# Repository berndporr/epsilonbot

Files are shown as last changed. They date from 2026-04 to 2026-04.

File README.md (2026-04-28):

# The Zeta-bot

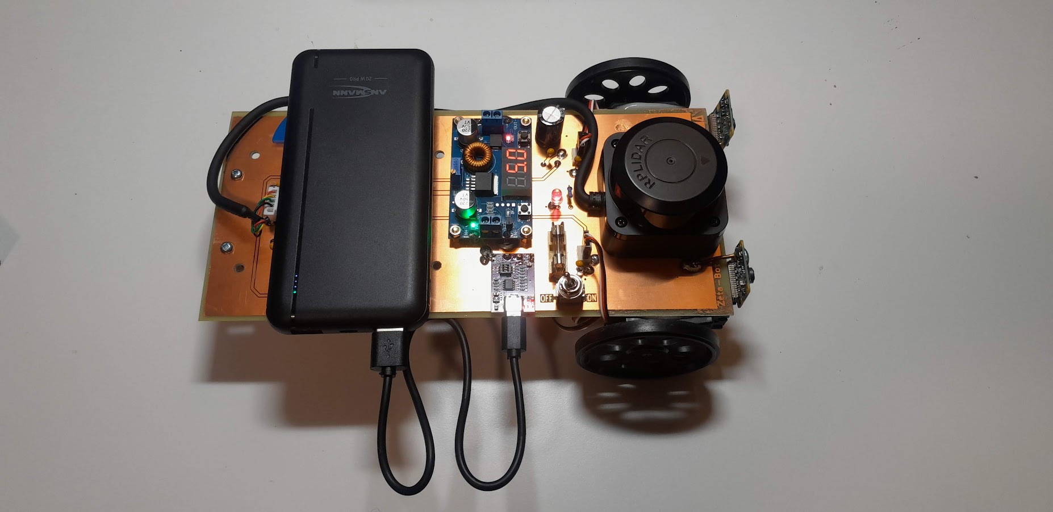
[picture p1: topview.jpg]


What is the Zeta-Bot?

The Zeta-Bot is an open-source robot platform that uses the:

 - Raspberry PI 5,
 - [Parallax's Continuous Rotation Servo Motors](https://www.parallax.com/product/parallax-continuous-rotation-servo/),
 - [C1 LIDAR](https://www.slamtec.com/en/c1),
 - two [Raspberry PI V2 cameras](https://www.raspberrypi.com/products/camera-module-v2/) for stereo vision,
 - [a standard mobile phone 1700mAh power bank](https://uk.rs-online.com/web/p/power-banks/2498449).

It's based on years and years of experience making single PCB
Raspberry PI based robots. Every part has been chosen because of
extensive lab use proving its reliability over the years and because
of its solid hard- and software support.

## Hardware

The KiCad design files and BOM are in [hardware](hardware).

## Software

It's all in C++! Both cameras and LIDAR have an event driven framework with callbacks so no loops and multi-threaded by design.

 - The motor control libraries are in [wheeleddrive](wheeleddrive).
 - The cameras driver is in https://github.com/berndporr/libcamera2opencv with a demo to display one camera and in [stereo](stereo) is a QT6 based stereo viewer and disparity detector.
 - The LIDAR driver is in https://github.com/berndporr/c1lidar

## Credits

 - (c) 2026, Bernd Porr, mail@berndporr.me.uk
 - (c) 2025, Saleh AlMulla
 - (c) 2025, Yixuan Zha

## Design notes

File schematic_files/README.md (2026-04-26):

# Schematic files

It's been designed by KiCad 10.

The design at the moment is according to GU's workshop requirements who cannot do solderstop and need 2mm pads.

The [bom](bom.pdf) is here.

The Linear servos are simply glued with epoxy onto the PCB.

The RPI V2 cameras are soldered on the ground plane of the PCB with two stiff 6mm wires. There seem to be no sensible camera holders about so stiff wires seem to be the best option also to adjust the cameras for stereo.

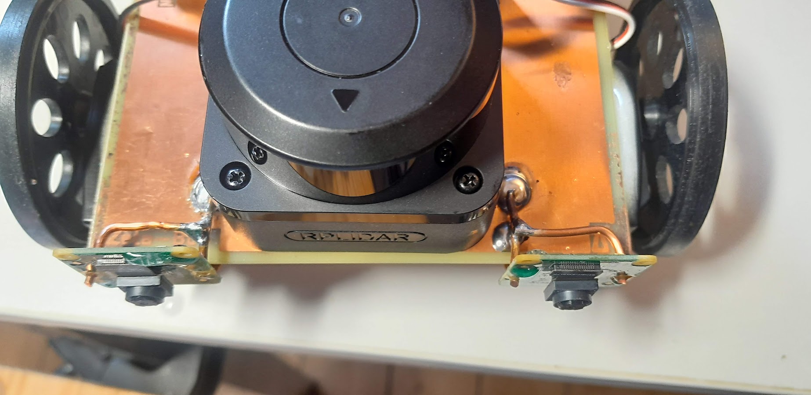
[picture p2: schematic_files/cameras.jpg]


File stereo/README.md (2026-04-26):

# Stereoviewer

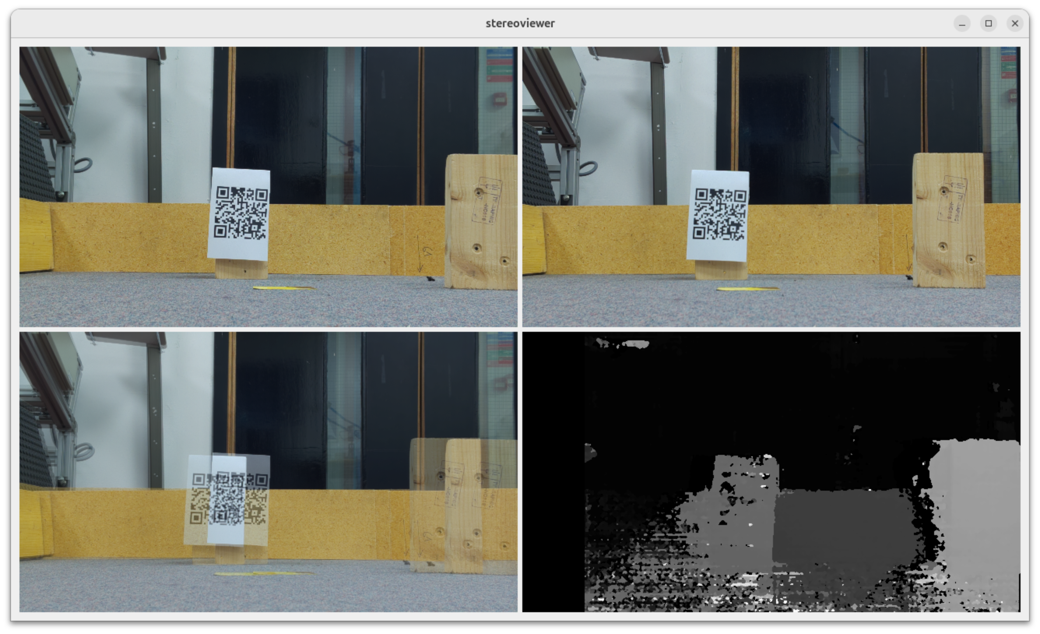
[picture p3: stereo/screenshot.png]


Simple QT6 demo application which captures from both cameras and then calculates
the disparity map.

## Prerequisites

```
apt install libopencv-dev libcamera-dev libturbojpeg0-dev
```

## Compilation

```
cmake .
make
```

## How to run

```
./stereoviewer
```

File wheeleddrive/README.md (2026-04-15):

# C++ ZetaBot API for the Raspberry PI 5

## Prerequisites

Add to `/boot/firmware/config.txt`:

```
dtoverlay=pwm-2chan
```

and reboot.

Check with:

```
pinctrl -p
```

that you see:

```
12: a3    pd | lo // GPIO18 = PWM0_CHAN2
35: a3    pd | lo // GPIO19 = PWM0_CHAN3
```

which corresponds to the sysfs files:

```
/sys/class/pwm/pwmchip0/pwm2: GPIO18 
/sys/class/pwm/pwmchip0/pwm3: GPIO19
```

### libgpiod

The GPIO pins are accessed via the C++ API of the `libgpiod`:

```
apt-get install libgpiod-dev
```

### ncurses

This is needed for testIO for a very simple ASCII GUI!

```
apt-get install libncurses-dev
```

## Building

The built system is `cmake`. Just type:
```
cmake .
make
sudo make install
```

## Usage

### Motor speed

Setting the speeds of the left/right wheels:
```
setLeftWheelSpeed(float speed);
setRightWheelSpeed(float speed);
```
where speed is between -1 and +1.

## Demo programs

 - `testIO` is a simple text GUI program to control the motors.
 - `testMotor` ramps up the motor speed and back again.

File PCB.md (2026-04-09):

# DeltaBot PCB Overview

The DeltaBot PCB was designed in **KiCad** with a double-sided layer layout. The design integrates key subsystems including the **Radxa ROCK 5B**, LiDAR sensor, camera module, and servo motors.

<p align="center">
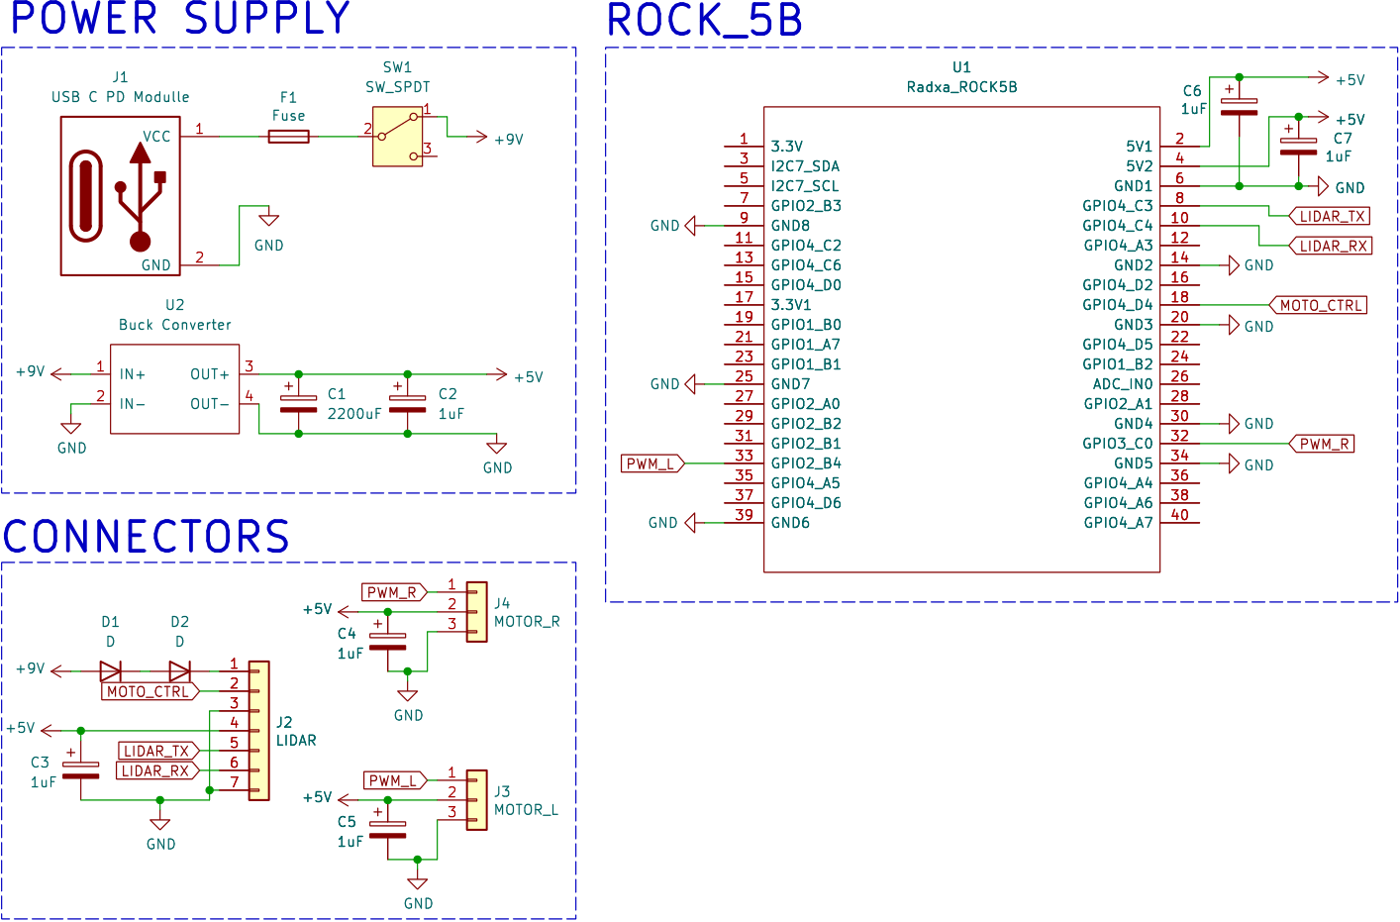
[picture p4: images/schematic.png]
  
</p>

---

## Power System
- Powered via **USB-C Power Delivery (PD)** module at **9V**, stepped down to **5V** using a **DC-DC buck converter**
- A **3.15A fuse** protects against overcurrent
- An **SPDT switch** provides manual ON/OFF control
- A **2200 µF capacitor** suppresses 5V rail ripple for improved voltage stability
- **1 uF** blocking capacitors between each POWER & GND

---

## PCB Layout (Front & Back Layers)

<p align="center">
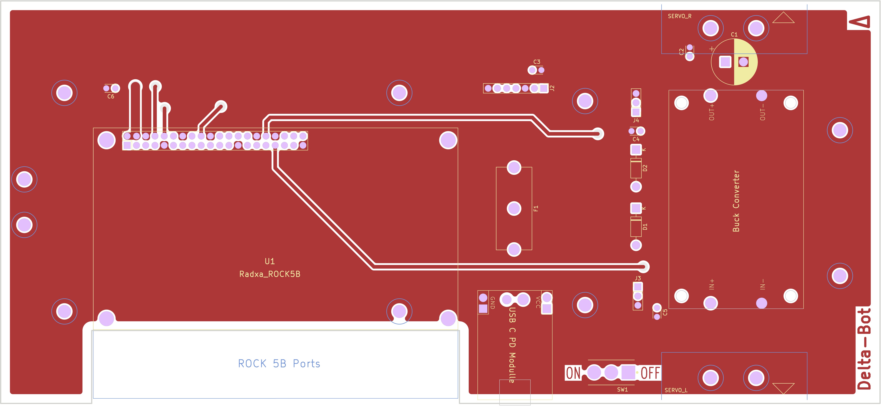
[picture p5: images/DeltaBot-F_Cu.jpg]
  
</p>
<p align="center">
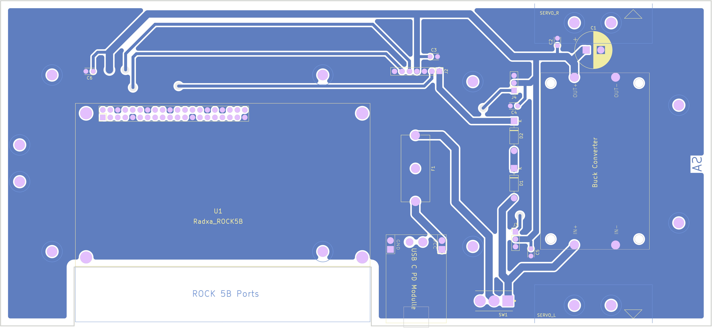
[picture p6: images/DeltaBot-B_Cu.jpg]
  
</p>

---

## ROCK 5B GPIO Pin Assignments

| Function | GPIO Pin(s) | Description |
|---|---|---|
| +5V Power | 2, 4 | Supplies power to board |
| GND | Multiple | Ground reference |
| UART_TX | 8 | TX to LiDAR's RX |
| UART_RX | 10 | RX from LiDAR's TX |
| NC | 18 | NC |
| PWM_L | 32 | PWM control for left servo |
| PWM_R | 33 | PWM control for right servo |

To change or add to the layout, check [here](https://wiki.radxa.com/Rock5/hardware/5b/gpio) for the rock's gpio connections.

---

## Connectors

- **J2 (LiDAR)**: 7-pin Molex
  - UART (TX/RX), 5V & 8.34V power lines
- **J3 / J4 (Servo Motors)**: 3-pin headers  
  - 5V, GND, PWM (Left/Right)

---

## Files

- [Full Schematic](schematic_files/DeltaBot.kicad_sch)
- [PCB Design](schematic_files/DeltaBot.kicad_pcb)
- [PCB Footprints](schematic_files/deltabot.pretty.zip)
- [Rock 5B KiCAD Symbol](schematic_files/deltabot.lib.kicad_sym)
  
---

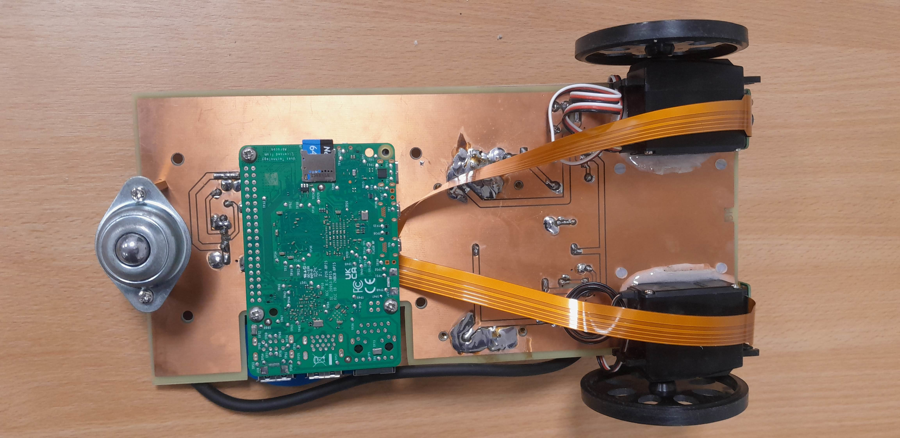
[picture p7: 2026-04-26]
hardware/bottomview.jpg

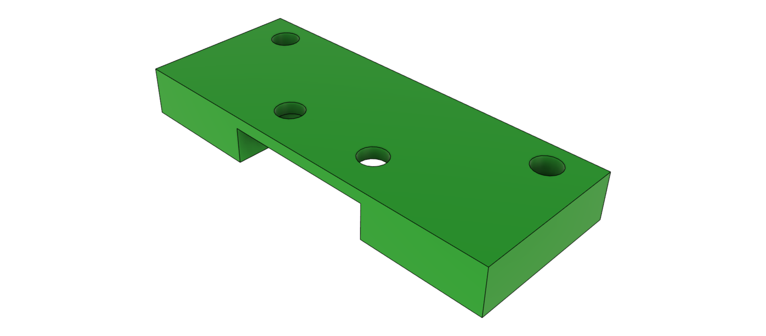
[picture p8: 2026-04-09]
images/ball.png

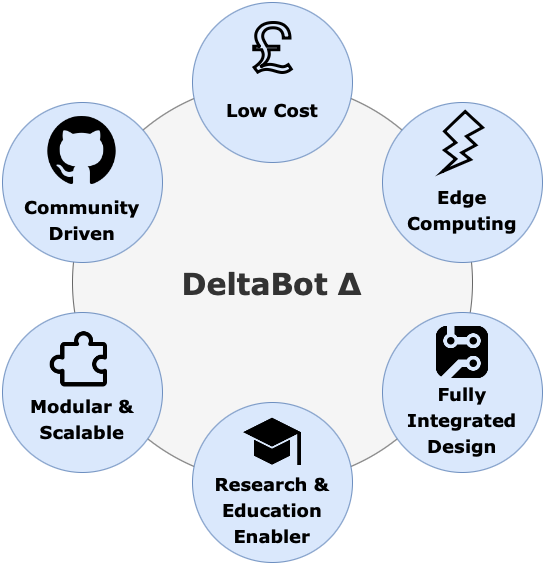
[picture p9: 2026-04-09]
images/goals.png

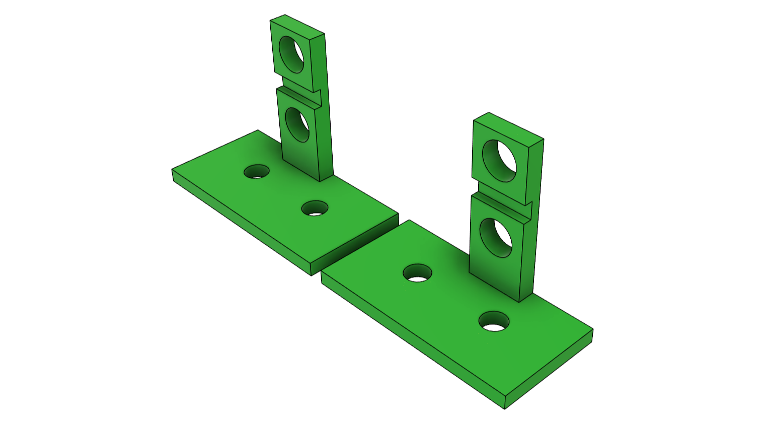
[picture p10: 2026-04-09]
images/bracket2.png

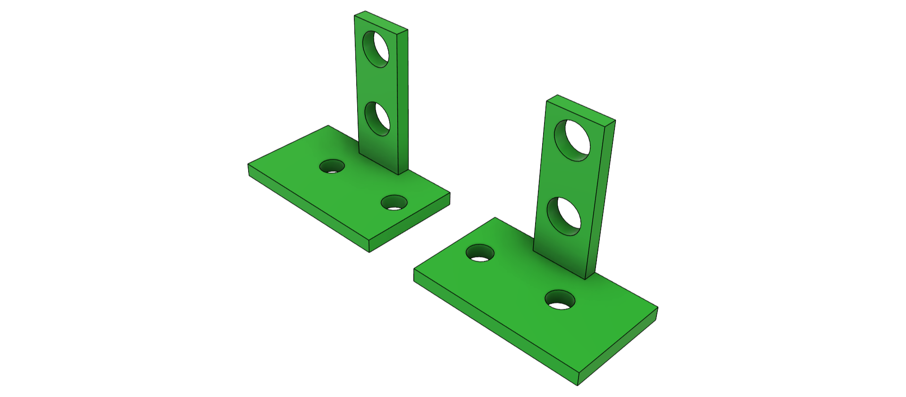
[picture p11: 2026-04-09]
images/bracket.png

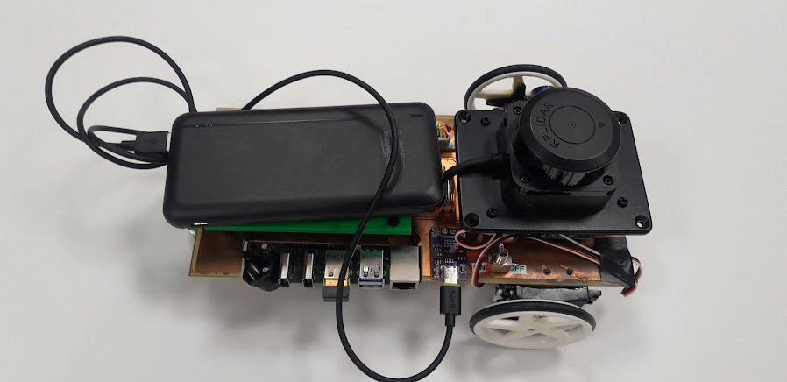
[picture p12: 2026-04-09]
images/deltabot.jpg

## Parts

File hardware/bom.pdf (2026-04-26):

ZetaBot

Id Designator | Footprint | Quantity
2 C1 | CP_Radial_D12.5mm_P5.00mm | 1
3 C2, C3, C4, C5, C6 C_Disc_D3.0mm_W2.0mm_P2.50mm | 5
4 D1 | LED_D5.0mm_Clear | 1
5 F1 | Fuseholder_Cylinder-5x20mm_Schurter_0031_8201_Horizontal_Open | 1
6 J1 | USB_C | 1
7 J2 | PinHeader_1x05_P2.54mm_Vertical | 1
8 J3 | PinHeader_1x03_P2.54mm_Vertical | 1
9 J4 | PinHeader_1x03_P2.54mm_Vertical | 1
10 R1 | R_Axial_DIN0207_L6.3mm_D2.5mm_P10.16mm_Horizontal | 1
11 SW1 | TE_4-1825136-5 | 1
12 U1 | RPLIDAR C1 | 1
13 U1 | RPI5 | 1
14 U2 | BUCK_CONV | 1
15 | Servo | 2
16 | RPI V2 Camera | 2
17 | Ball castor with 2-hole fastening | 1

Designation | Supplier and ref
2200uF/Electr | any
1uF/Tantalum | any
LED | any
Fuse | any
USB C PD Modulle
Conn_01x05 | any
MOTOR_L | any
MOTOR_R | any
330R | any
SW_SPDT | any
RPLIDAR C1
RPI5 | Raspberry
Buck Converter
Parallax Cont Rotat Servo https://www.parallax.com/product/parallax-continuous-rotation-servo/
Raspberry PI V2 Camera
Any small ball castor | https://www.esska-tech.co.uk/shop/Ball-castors-with-2-hole-fastening-Load-capacity-25-to-55-kg--952914741000-25890

https://www.amazon.com/ACEIRMC-Trigger-Polling-Detector-Notebook/dp/B0BTHXKM91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

https://www.slamtec.com/en/c1

https://thepihut.com/products/20w-adjustable-dc-dc-buck-converter-with-digital-display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

https://www.raspberrypi.com/products/camera-module-v2/

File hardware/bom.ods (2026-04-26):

Id | Designator | Footprint | Quantity | Designation | Supplier and ref
2 | C1 | CP_Radial_D12.5mm_P5.00mm | 1 | 2200uF/Electr | any
3 | C2, C3, C4, C5, C6 | C_Disc_D3.0mm_W2.0mm_P2.50mm | 5 | 1uF/Tantalum | any
4 | D1 | LED_D5.0mm_Clear | 1 | LED | any
5 | F1 | Fuseholder_Cylinder-5x20mm_Schurter_0031_8201_Horizontal_Open | 1 | Fuse | any
6 | J1 | USB_C | 1 | USB C PD Modulle | https://www.amazon.com/ACEIRMC-Trigger-Polling-Detector-Notebook/dp/B0BTHXKM91
7 | J2 | PinHeader_1x05_P2.54mm_Vertical | 1 | Conn_01x05 | any
8 | J3 | PinHeader_1x03_P2.54mm_Vertical | 1 | MOTOR_L | any
9 | J4 | PinHeader_1x03_P2.54mm_Vertical | 1 | MOTOR_R | any
10 | R1 | R_Axial_DIN0207_L6.3mm_D2.5mm_P10.16mm_Horizontal | 1 | 330R | any
11 | SW1 | TE_4-1825136-5 | 1 | SW_SPDT | any
12 | U1 | RPLIDAR C1 | 1 | RPLIDAR C1 | https://www.slamtec.com/en/c1
13 | U1 | RPI5 | 1 | RPI5 | Raspberry
14 | U2 | BUCK_CONV | 1 | Buck Converter | https://thepihut.com/products/20w-adjustable-dc-dc-buck-converter-with-digital-display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
15 |  | Servo | 2 | Parallax Cont Rotat Servo | https://www.parallax.com/product/parallax-continuous-rotation-servo/
16 |  | RPI V2 Camera | 2 | Raspberry PI V2 Camera | https://www.raspberrypi.com/products/camera-module-v2/
17 |  | Ball castor with 2-hole fastening | 1 | Any small ball castor | https://www.esska-tech.co.uk/shop/Ball-castors-with-2-hole-fastening-Load-capacity-25-to-55-kg--952914741000-25890

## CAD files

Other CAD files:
additional_files/deltabot.f3z

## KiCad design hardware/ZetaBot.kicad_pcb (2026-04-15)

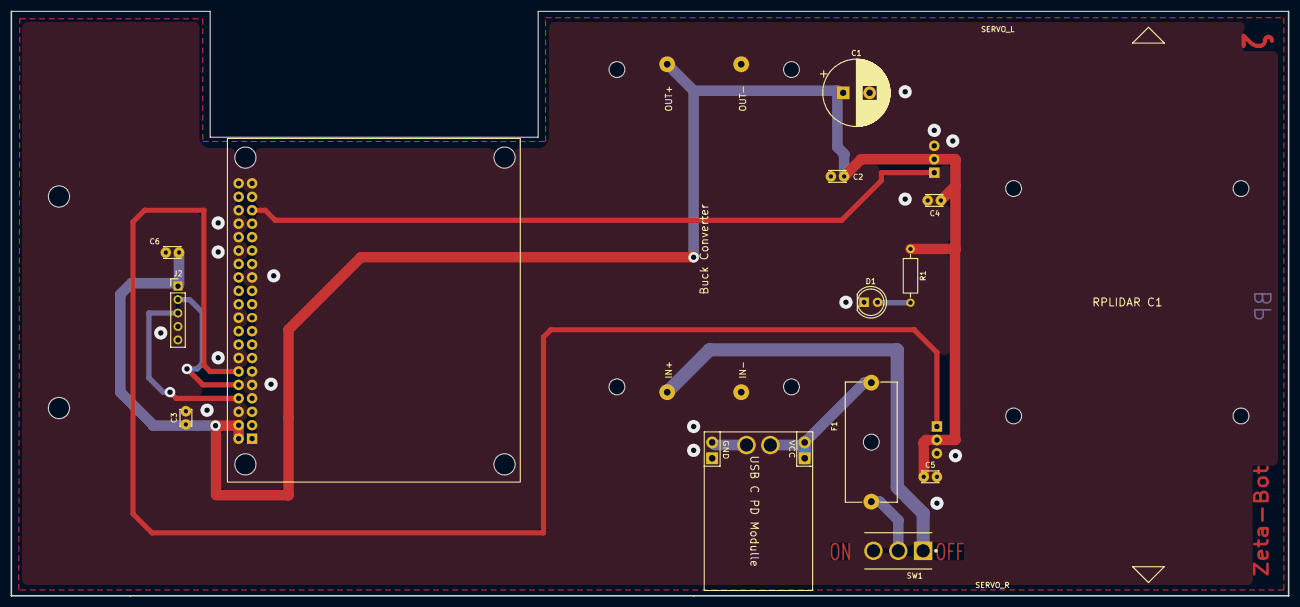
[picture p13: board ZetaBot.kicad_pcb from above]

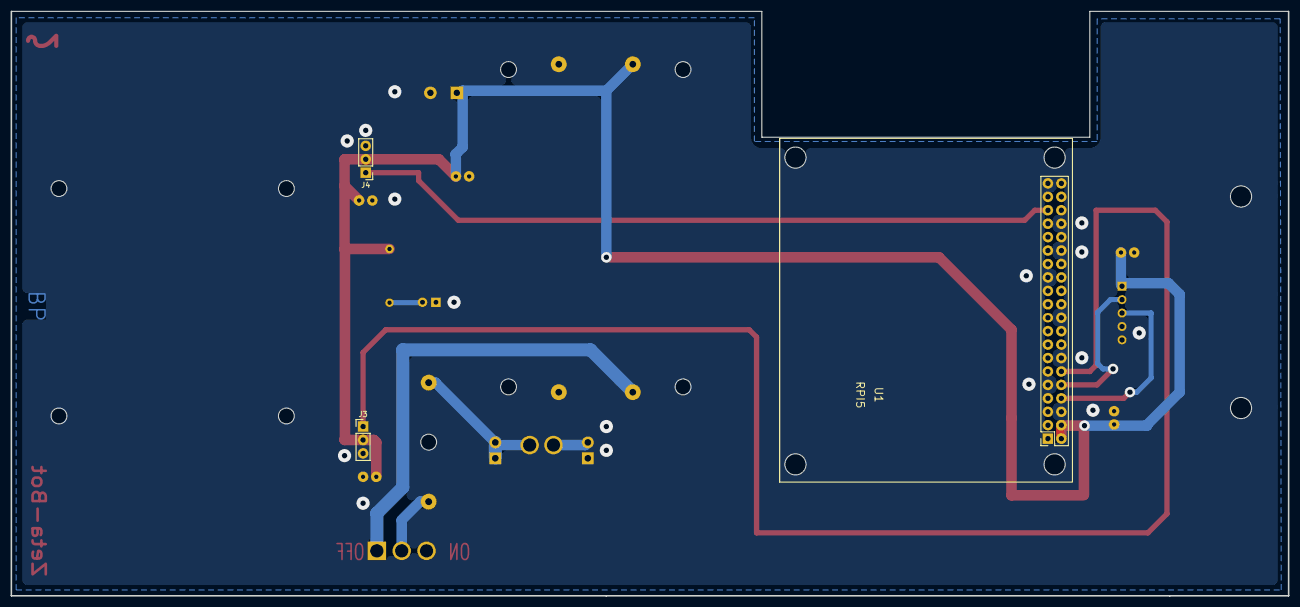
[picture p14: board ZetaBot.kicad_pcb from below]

Board: 2 copper layers, 241.5 x 110.5 mm, 17 parts (3 on the bottom side), 10 nets.

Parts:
C1: 2200uF; CP_Radial_D12.5mm_P5.00mm
C2, C3, C4, C5, C6: 1uF; C_Disc_D3.0mm_W2.0mm_P2.50mm
D1: LED; LED_D5.0mm_Clear
F1: Fuse; Fuseholder_Cylinder-5x20mm_Schurter_0031_8201_Horizontal_Op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
J1: USB C PD Modulle; USB_C
J2: Conn_01x05; PinHeader_1x05_P2.54mm_Vertical
J3: MOTOR_L; PinHeader_1x03_P2.54mm_Vertical
J4: MOTOR_R; PinHeader_1x03_P2.54mm_Vertical
R1: 330R; R_Axial_DIN0207_L6.3mm_D2.5mm_P10.16mm_Horizontal
SW1: SW_SPDT; TE_4-1825136-5
U1: RPLIDAR C1
U1#2: RPI5
U2: Buck Converter; BUCK_CONV

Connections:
+5V: C1.1, C2.1, C3.1, C4.1, C5.1, C6.1, J2.1, J3.2, J4.2, R1.1, U1#2.2 (5V1), U1#2.4 (5V2), U2.3 (OUT+)
+9V: SW1.1 (A), U2.1 (IN+)
GND: C1.2, C2.2, C3.2, C4.2, C5.2, C6.2, D1.1 (K), J1.2 (GND), J1.4 (GND), J2.4, J3.3, J4.3, U1#2.6 (GND1), U1#2.9 (GND8), U1#2.14 (GND2), U1#2.20 (GND3), U1#2.25 (GND7), U1#2.30 (GND4), U1#2.34 (GND5), U1#2.39 (GND6), U2.2 (IN-), U2.4 (OUT-)
LIDAR_RX: J2.3, U1#2.8 (GPIO14_UART/TX)
LIDAR_TX: J2.2, U1#2.10 (GPIO15_UART/RX)
unnamed: D1.2 (A), R1.2
unnamed: F1.2, J1.1 (VCC), J1.3 (VCC)
unnamed: F1.1, SW1.2 (B)
PWM_L: J4.1, U1#2.35 (GPIO19_PWM0/CHAN2)
PWM_R: J3.1, U1#2.12 (GPIO18_PWM0/CHAN2)

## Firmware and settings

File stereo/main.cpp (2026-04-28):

#include "window.h"
#include <QApplication>
#include <opencv2/opencv.hpp>
#include <libcamera/libcamera/camera_manager.h>

// Main program
int main(int argc, char *argv[])
{
	QApplication app(argc, argv);

	libcamera::CameraManager cm;
	cm.start();

	// create the window
	Window window;
	window.show();

	Libcam2OpenCV cameraL;
	cameraL.registerCallback([&](const cv::Mat &mat, const libcamera::ControlList &)
							 { 
								window.updateImageL(mat); });

	Libcam2OpenCV cameraR;
	cameraR.registerCallback([&](const cv::Mat &mat, const libcamera::ControlList &)
							 { 
								window.updateImageR(mat); });

	Libcam2OpenCVSettings settings;
	settings.width=1920;
	settings.height=1080;
	settings.cameraIndex = 0;
	cameraL.start(cm, settings);
	settings.cameraIndex = 1;
	cameraR.start(cm, settings);

	// execute the application
	const int r = app.exec();

	cameraL.stop();
	cameraR.stop();
	cm.stop();
	return r;
}

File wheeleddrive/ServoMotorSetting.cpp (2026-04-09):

#include "ServoMotorSetting.h"

int ServoMotorSetting::start(int channel, int chipNo)
{
    return pwm.start(channel, low_time, high_time, chipNo);
    setSpeed(0);
}

ServoMotorSetting::~ServoMotorSetting()
{
    stop();
}

int ServoMotorSetting::speedToHighTime(float speed) // speed range from -1 to 1, 0 is stop
{
    if (speed > 1)
        speed = 1;
    if (speed < -1)
        speed = -1;
    int neutral_time = 1524000; // When speed is 0, The high time is 1524000
    int step_size = 100000;

    return neutral_time + (speed * step_size);
}

int ServoMotorSetting::setSpeed(float speed)
{
    int r;
    int high_time = speedToHighTime(speed);
    int per = INVERSEDUTY + high_time;
    r = pwm.setPeriod(per);
    if ( r < 0 ) {
	fprintf(stderr,"Cannot set period.\n");
	return r;
    }
    r = pwm.setDutyCycleNS(INVERSEDUTY);
    if ( r < 0 ) {
	fprintf(stderr,"Cannot set duty cycle.\n");
    }
    return r;
}

int ServoMotorSetting::stop()
{
    int r;
    r = setSpeed(0);
    if (r < 0) {
	fprintf(stderr,"Could not set speed to zero.\n");
    }
    r = pwm.disable();
    if (r < 0) {
	fprintf(stderr,"Could not disable the PWM.\n");
    }
    return r;
}

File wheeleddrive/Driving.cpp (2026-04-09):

#include "Driving.h"

void Driving::start()
{
    int r = 0;
    r = leftMotor.start(leftChannel, leftChipNo);
    if (r < 0) {
	stop();
	throw std::runtime_error("Driving: could not start the left motor!");
    }
    r = rightMotor.start(rightChannel, rightChipNo);
    if (r < 0) {
	stop();
	throw std::runtime_error("Driving: could not start the right motor!");
    }
    setMotorSpeeds(0,0);
}

void Driving::stop()
{
    leftMotor.setSpeed(0);
    rightMotor.setSpeed(0);
    leftMotor.stop();
    rightMotor.stop();
}

int Driving::setMotorSpeeds(float left_speed, float right_speed)
{
    int r = 0;
    r = leftMotor.setSpeed(left_speed);
    if (r < 0) {
	fprintf(stderr,"Could not set left motor speed.\n");
	return r;
    }
    r = rightMotor.setSpeed(-right_speed);
    if (r < 0) {
	fprintf(stderr,"Could not set right motor speed.\n");
	return r;
    }
    return r;
}

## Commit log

2026-04-09 Initial commit which is still the deltabot!
    [EpsilonBot.kicad_pcb, EpsilonBot.kicad_sch, deltabot.f3z]
2026-04-09 Updated PCB layout for the RPI
    [EpsilonBot.kicad_pcb, EpsilonBot.kicad_sch]
2026-04-12 Added missing files
    [EpsilonBot.kicad_pcb, EpsilonBot.kicad_sch]
2026-04-12 Added a new footprint for the USB C PD.
    [ZetaBot.kicad_pcb, ZetaBot.kicad_sch]
2026-04-14 Added PDF
    [ZetaBot-NPTH.drl, ZetaBot-PTH.drl]
2026-04-15 Added readme
    [ZetaBot.kicad_pcb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]
2026-04-26 Added info about the schematic.
    [bom.ods]
2026-04-26 Changed it to "hardware".
    [ZetaBot.kicad_pcb, ZetaBot.kicad_sch, bom.ods]
2026-05-12 added a half-baked program to test wheel speed. Need to get rubber coats for wheels

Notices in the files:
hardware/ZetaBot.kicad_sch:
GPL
